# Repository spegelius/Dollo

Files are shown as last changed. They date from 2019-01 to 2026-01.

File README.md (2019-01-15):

# Dollo3D
A (almost) fully printed 3D printer, that scales.

# Goals in order of priority

1) Make a 3D printer that can make as many of its own parts as possible

2) Have it so the machine can scale with little to no throwing away of old parts

3) Make it easy to assemble

4) Use no more than a single 1KG spool of plastic to make. (not happening)

5) Make it as low cost as possible.

6) use parts that are easy to find.

7) make it durable (since it can print its own parts this isn't super high priority)

8) hope people stop asking "what if you could 3D print a 3D printer" because of course you can and its not that unique of an idea

# Part count and list for smallest viable Dollo, with around 21x21x12cm print volume. Smaller frame can be built, but the z-axis parts aren't tested in any way with that kind of setup

* 26 -- extention.stl
* 4 -- extention_90_bend.stl (or extention_90_bend_extra_stiff.stl)
* 8 -- corner.stl (or corner_extra_stiff.stl)
* 192+ -- bow_tie.stl but extra never hurts (or bow_tie_with_brim.stl)
* 132+ —- long_tie.stl (or long_tie_split.stl, more forgiving on the tolerances)
* 10+ -- long_tie_half.stl
* 50+ -- long_bow_tie.stl (or long_bow_tie_split.stl, more forgiving on the tolerances)
* 2 -- x_spacer.stl
* 6 -- rack_5.stl
* 6 -- rack_dove_pin.stl 
* 1 -- bed_carriage_endstop_screw.stl
* 1 -- bed_carriage_endstop_screw_mount.stl
* 1 -- bed_carriage_endstop_screw_nut.stl
* 4 -- bed_carriage_rail.stl
* 4 -- bed_carriage_rail_short.stl
* 4 -- bed_carriage_rail_center.stl
* 2 -- bed_carriage_rail_frame_mount.stl
* 2 -- bed_carriage_rail_frame_mount_top.stl
* 4 -- bed_carriage_rail_slide.stl
* 2 -- bed_screw_housing.stl
* 2 -- bed_screw_housing_coupler.stl
* 2 -- bed_screw_housing_top.stl
* 10+ -- cable_clip_large.stl/cable_clip_small.stl
* 1 -- cable_shroud_frame_mount.stl (if using cable shroud)
* 1 -- hot_end_mount.stl
* 1 -- hot_end_mount_clamp.stl (or hot_end_mount_clamp_shroud_mount.stl if using cable shroud)
* 1 -- hot_end_mount_fan_duct.stl
* 1 -- hot_end_mount_prox_sensor_clamp.stl (if using proximity sensor)
* 4 -- leg.stl
* 4 -- leg_foot.stl OR following 3 items.
* 4 -- leg_foot_adjustable.stl
* 4 -- leg_foot_adjustable_core.stl
* 4 -- leg_foot_dampener.stl (print with flex material)
* 3 -- motor_gear.stl (or motor_gear_slop_0.1.stl)
* 6 -- motor_mount_small.stl
* 1 -- psu_holder.stl OR following 3 parts if using ATX psu
* 1 -- psu_holder_atx_psu_cover.stl
* 1 -- psu_holder_back_atx.stl
* 1 -- psu_holder_front_atx.stl
* 1 -- psu_holder_clip_extension.stl
* 2 -- xy_endstop_rackend.stl OR
* 2 -- xy_endstop_racktop.stl (I prefer this, easier to adjust position)
* 1 -- z_endstop.stl
* 2 -- z_screw_120.stl
* 2 -- z_screw_center_coupler.stl
* 2 -- z_screw_motor_coupler_flex.stl
* 2 -- z_coupler_flexible_coupler_nut_hex.stl
* 2 -- z_coupler_flexible_coupler_tube.stl (print with flex material)
* 2 -- z_coupler_motor_shaft_adapter.stl
* 6 -- z_screw_housing_bolt_side.stl
* 6 -- z_screw_side_roller.stl
* 6 -- z_screw_side_roller_axle.stl
* 6 -- z_screw_side_roller_axle_washer.stl
* 1 -- ramps_mount.stl
* 2 -- ramps_mount_fan_mount_60mm.stl
* 3 -- ramps_mount_frame_clip.stl
* 2 -- tools/rail_jig.stl
* 2 -- tools/rail_jig_clip.stl
* 1 -- tools/z_screw_jig.stl
* 2 -- tools/z_screw_jig_clip.stl

# Metal parts we might get rid of in the future

* 9 -- M3x40  for the motor mounts
* 8 -- M3x10  for the z motors

# Electronics and other

* 1 - main controller board. Frame mount parts for RAMPS are available. Also for Raspi3
* 3 - end stop switches
* 5 - steppermotors , no need for very beefy motors
* 1 - hotend or whatever tool tip you want really. E3Dv6 is tested
* 1 - hobbed thing, gear or bolt. Actually whole extruder. Buy or pick one to print from thingiverse. This is good: https://www.thingiverse.com/thing:2243325
* 1 - heated bed (21x21cm)
* 1 - glass/aluminum that fits on the bed (depends if the bed needs one)
* 4 - springs and screw for leveling your bed.
* some glue for joining the bed_carriage_rail and z_screw parts together

# Options for a larger printer

* the default expansion length in each direction is 12cm (default extention part length).
* the frame can be extended in any direction, just print enough extention.stl parts and ties. If extending in z-direction, also print enough bed_carriage_rail, bed_carriage_rail_center, z_screw_120, z_screw_center
* the default 12cm expansion length can be adjusted to suit ones need, just modify the scad files and export different length models (make sure all updated models are same length)
* the frame will become somewhat wobbly after certain z-height (25+cm). There are stabilizer parts designed, but not for the current Dollo iteration. WIP currently

# Print settings
1. I use PLA for most of the parts, except PETG for rack_5, all _tie-parts and z_screw_side_roller. Flexible material (FilaFlex or similar) for few models (see BOM). Nylon for the part cooling (hotend) fan
2. For most parts, 2x perimeter, 20% infill, 0.2mm layer height, outer perimeter first and no supports. Some models do need supports, but those should be easy to spot.
3. Motor_gear: 4+ perimeters, 90% infill
4. bed_carriage_rails, centers, z_screws: 3 perimeters, 25+% infill
5. All _tie parts: print only after printing at least 1 extention. Print few of each _tie part and see how they fit. Most likely you'll need to use scaling in slicer sw to get them fit.

# How to assemble (mostly old info, needs update)
1) start with the basic frame, take a single corner and butt joint all 3 extension pieces to it with all 4 bow_tie slots. then on the end of each of those add corner pieces then extension pieces again until you have built out a full cube shape.

2) put on the racks. first you need to decide what side you want to be up, this really doesn't matter since it should be the same on all sides. Once you have figured that out, you can start putting your slots on the top of your printer with more bow ties add racks on parallel sides and to the top of your remaining extension piece. each should have 3 racks on it.

3) mounting your motors. first you will need to put a gear.scad on your motor shaft, then you can take a motor and put the motor_mount_small on it and screw in the single counter sunk screw on the bottom using a M3x10 and then put it on your printer rack and make sure the gear aligned with the rack teeth. once it does you can keep it on the rack and screw in your other motor_mount_small to the other side. (make sure to do this on the printer because if you don't it wont go on after) do this for all 3 racks and make sure the motor faces out.

4) mounting the x axis. grab your x_spacer and put them on the end of what you already have assembled on the left over extention piece and then slide that into the motor mount on each side of the printer.

5) Get the frame ready for the bed. first you need to prep you printer by taking the crazy looking twist_corner pieces and bow tie them to the inside of the printers frame mirroring each other but keep the bottom one out on each side.

6) now take a motor and mount put the gear_one on it and mount that to your bed, then take your middle_gear and put those next to the motor and then put your large_gear and large_twist together, and put those next in line. 

7) putting the bed in. This can be kind of tricky, but you have to twist your bed so it goes inside the frame sideways and the you should be-able to twist it to make it fit in the frame with the corners sticking out. and this is why we didn't put in the bottom corner_twists, because now your bed sits just under them and once you have the electronics set up it will be able to twist into those and once its in the teeth you will be able to add your last parts under it.

8) Electricity is fun. take all of your motor and put them into the correct stepper controllers making sure that your Y motors are plugged in opposite of each other. Plug in your electronics and make sure to upload the correct Dollo version of marlin. Once you have done this you should be able to move your motors and this is where you move your z motor in the negative direction (negative because that make the hotend and the bed closer) and once it is up at the top, you can put your last twist_corners on your printer.

9) hot ends and end stops. at the point of making this commit I do not yet have the end stops figured out. But the hotend should put in your hotend mount and should just slide and clip into your x motor mount. 

10) setting up the extruder. Not sure what extruder we are going to use yet, but if you have done 3D printing before you should know how all of that works and be able to get it going.

Z options) I do have the z axis all modeled for being fully printed and able to scale

# Extra cool facts

1) I came up with the original version of this when I was 16 and in high school and it was done in blender because thats all I knew how to use

2) This printer as it stands is under 1KG of printed parts 

3) We printed the first Dollo on 3 Prusa Mendal printer that were printer on other printers them selves and so on, all the way back to the start, so these machine have only open-source in their genealogy

4) I lived 300 miles from the printer that I used and did all of the printing over the internet using octopi to print the first Dollo

5) The Dollo can (if you want) have a metal core structure, we built it in just in case and it saved plastic so it was a win win.

6) The Dollo was made by a me and my dad, I didn't the modeling and he helped me come up with ideas on how to fix the issues I has on the way, and he test fit most of the pieces (the printers were at his house)

7) The Dollo has swappable tool heads so you can mill metal parts if you want!

8) We had no plans on how this was going to work before starting. We have gone through probably close to a 50 different ideas on how this thing should even work.

9) Half way though we almost gave up on the z and made the Dollo a Delta style printer (might still have something like that in the future)

10) We looked at a lot of other peoples printer before we could figure out how to do this one, we really could not have done it with out the community.

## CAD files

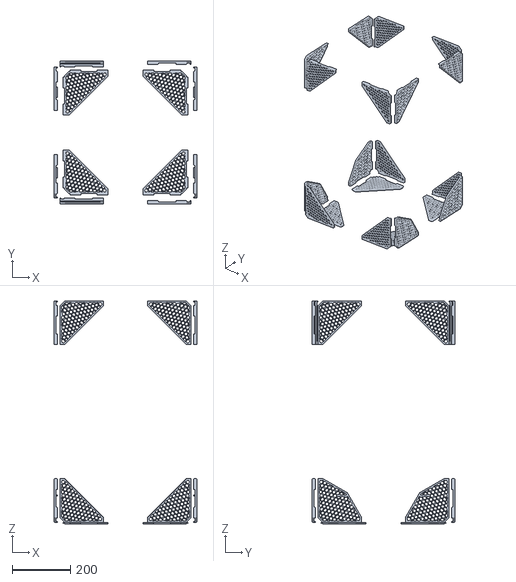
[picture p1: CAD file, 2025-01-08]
NEW_long_ties/mockup_stl/stabilizers_360_360_670_150.stl
490.0 x 490.0 x 766.0

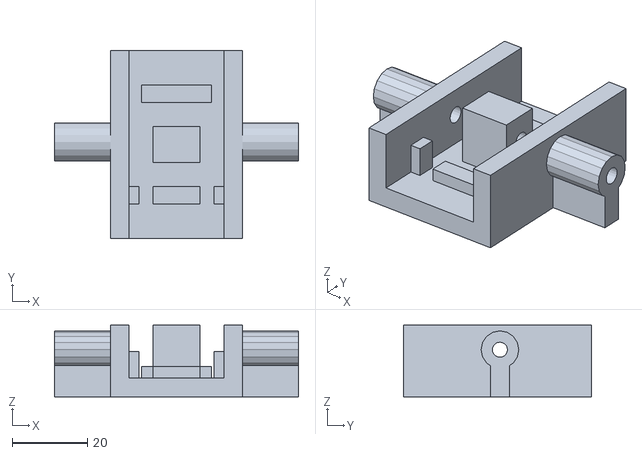
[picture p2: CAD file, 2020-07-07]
NEW_long_ties/STL/hacks/chain_link_drill_jig_4mm.stl
64.8 x 50.0 x 19.0

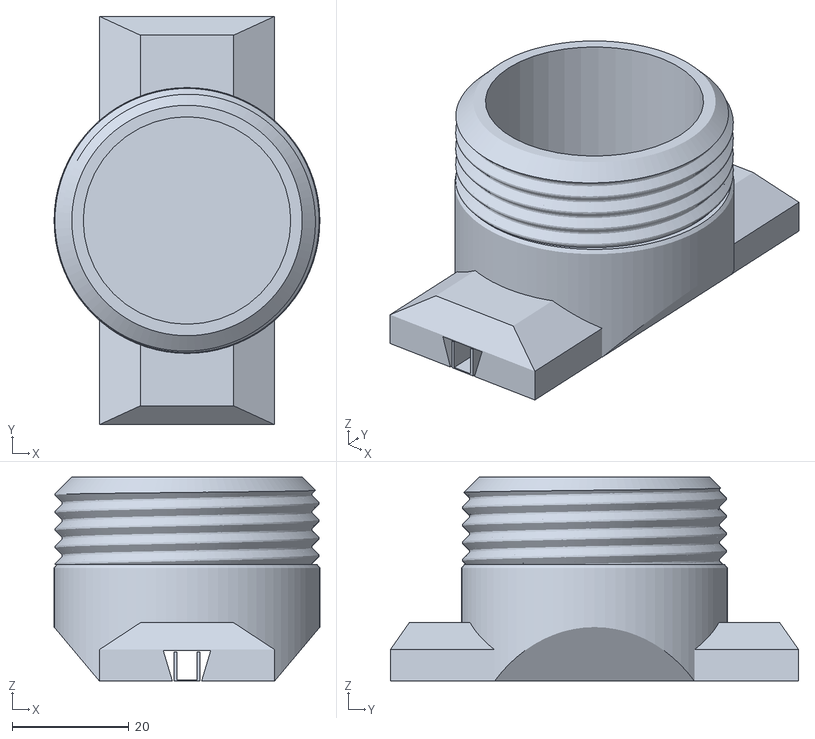
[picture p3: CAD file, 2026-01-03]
NEW_long_ties/STL/leg_middle_medium_adjustable.stl
45.6 x 70.0 x 35.0

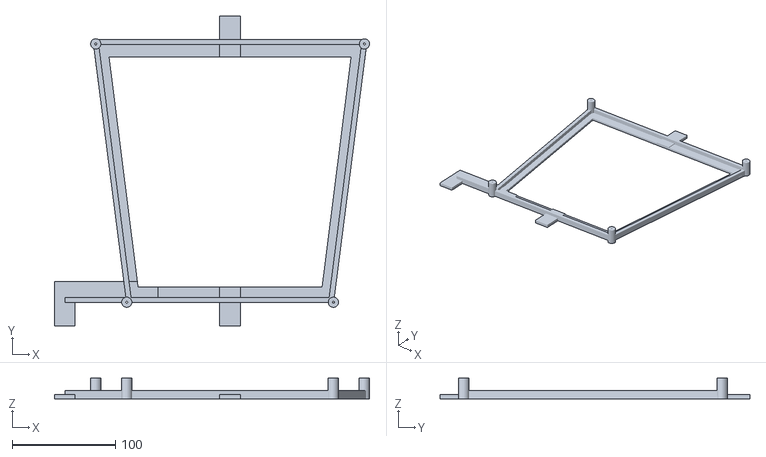
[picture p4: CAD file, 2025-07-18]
NEW_long_ties/STL/tools/bed_340_300_drill_jig.stl
305.0 x 300.0 x 20.0

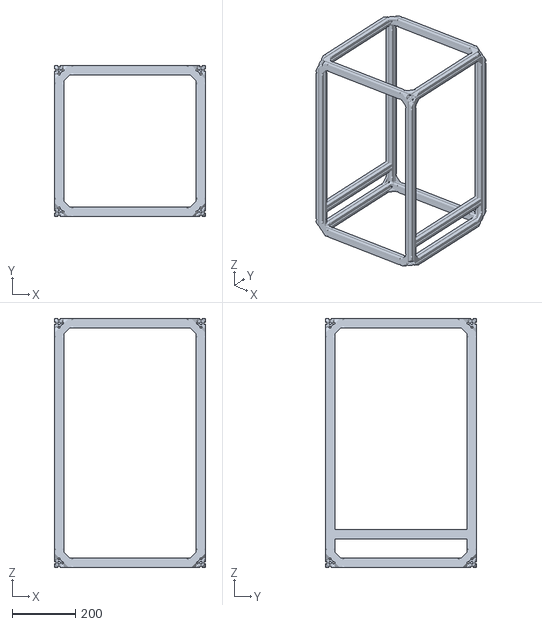
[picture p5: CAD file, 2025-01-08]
NEW_long_ties/mockup_stl/frame_360_360_670.stl
480.0 x 480.0 x 790.0

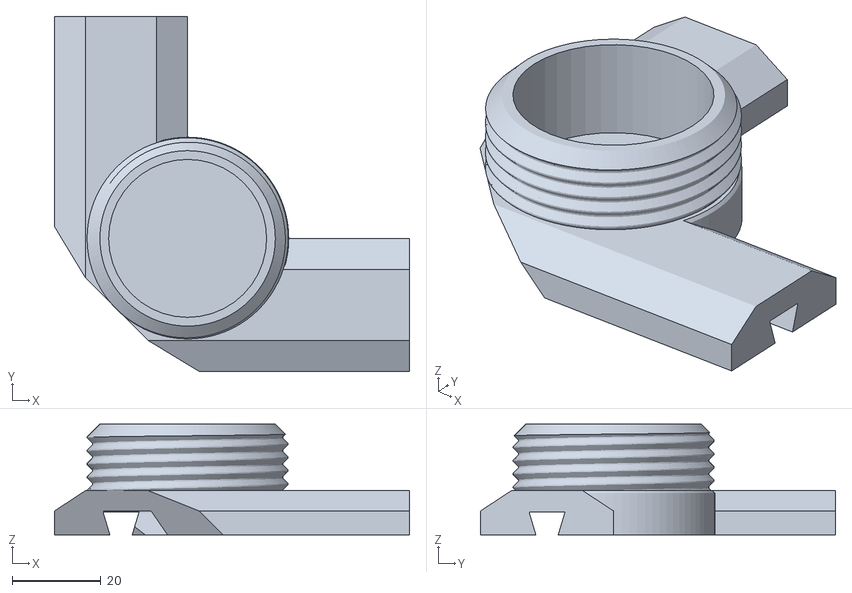
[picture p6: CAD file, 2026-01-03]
NEW_long_ties/STL/leg_small_adjustable_no_supports.stl
80.0 x 80.0 x 25.0

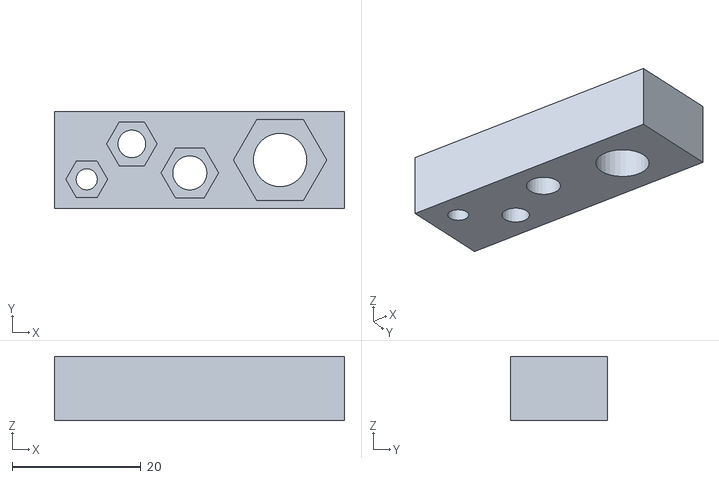
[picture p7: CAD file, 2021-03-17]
NEW_long_ties/STL/tools/test_nuts.stl
45.0 x 15.0 x 10.0

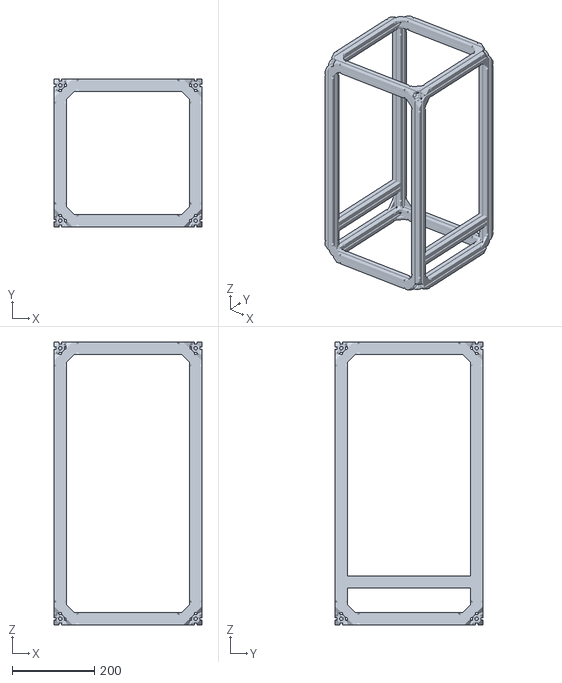
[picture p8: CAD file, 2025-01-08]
NEW_long_ties/mockup_stl/frame_240_240_570.stl
360.0 x 360.0 x 690.0

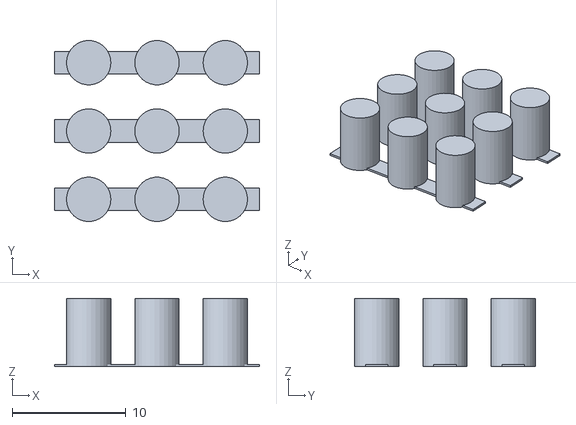
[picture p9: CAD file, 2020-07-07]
NEW_long_ties/STL/hacks/chain_link_drill_jig_nubs.stl
18.0 x 15.9 x 6.00

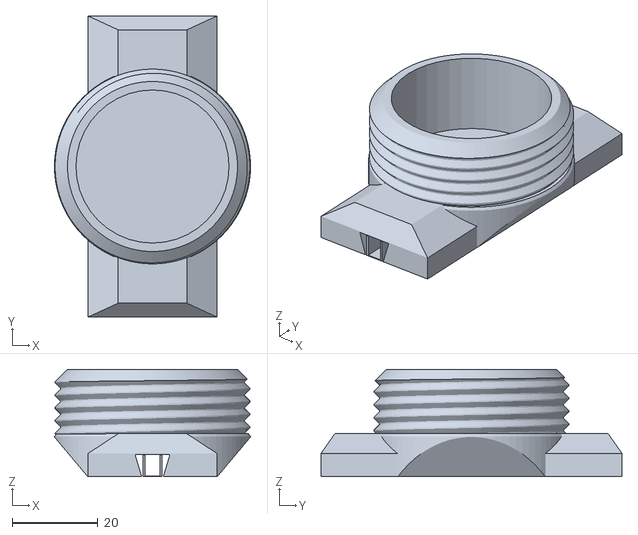
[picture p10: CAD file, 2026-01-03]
NEW_long_ties/STL/leg_middle_small_adjustable.stl
45.6 x 70.0 x 25.0

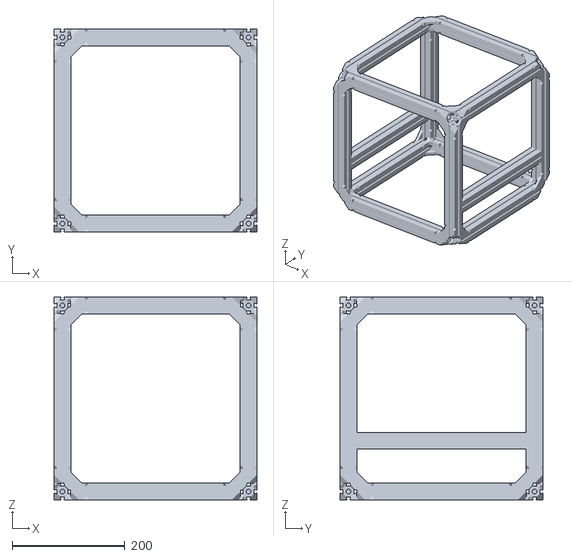
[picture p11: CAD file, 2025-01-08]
NEW_long_ties/mockup_stl/frame_240_240_240.stl
360.0 x 360.0 x 360.0

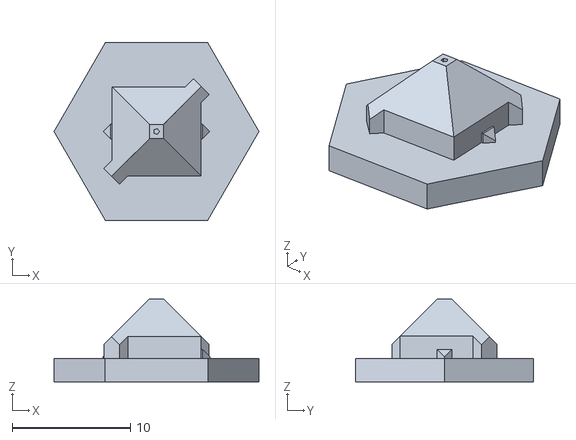
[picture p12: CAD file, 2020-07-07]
NEW_long_ties/STL/hacks/bed_carriage_rail_gap_plug.stl
17.3 x 15.0 x 7.00

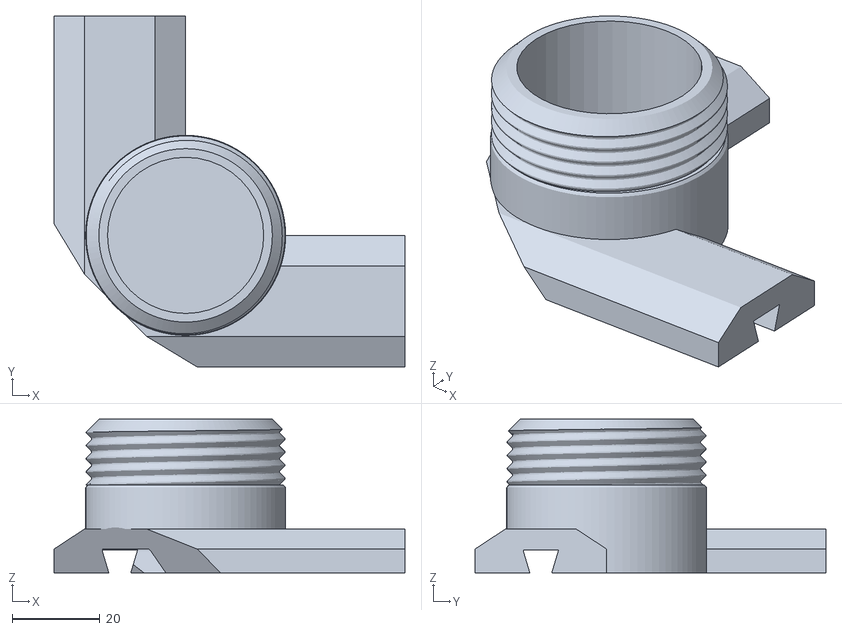
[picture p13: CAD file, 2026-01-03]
NEW_long_ties/STL/leg_medium_adjustable_no_supports.stl
80.0 x 80.0 x 35.0

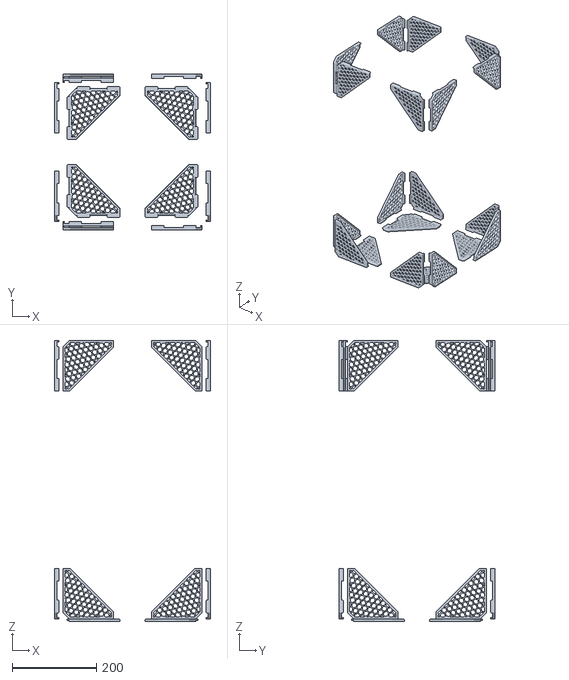
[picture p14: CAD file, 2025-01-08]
NEW_long_ties/mockup_stl/stabilizers_240_240_570_120.stl
370.0 x 370.0 x 666.0

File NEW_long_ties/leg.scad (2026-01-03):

include <globals.scad>;
include <include.scad>;

use <cable_clip.scad>;
use <extention.scad>;
use <mockups.scad>;
use <z_coupler.scad>;
use <z_screw.scad>;


////// VARIABLES //////

// core settings
pitch = 3;
dia_adjustable_inner = 45.9 - 0.3;
dia_adjustable_outer = 45.9 + 0.2;
echo("Adjustable dias:");
echo(dia_adjustable_inner, dia_adjustable_outer);

screw_steps = 100;


////// VIEW //////
//debug_leg_z();

//leg();
//leg_small_adjustable(render_threads=true);
//leg_small_adjustable(supports=false, render_threads=true);
//leg_small_adjustable(render_threads=false);

//leg_medium_adjustable(render_threads=true);
//leg_medium_adjustable(supports=false, render_threads=true);
//leg_medium_adjustable(render_threads=false);

//leg_middle_small_adjustable(render_threads=true);
//leg_middle_small_adjustable(render_threads=false);

leg_middle_medium_adjustable(render_threads=true);
//leg_middle_medium_adjustable(render_threads=false);

//leg_z();
//foot();
//foot_small();
//foot_adjustable_core();
//foot_adjustable();
//foot_dampener();

//test_adjustable_threads();


////// MODULES //////
module debug_leg_z() {
    intersection() {
        union() {
            leg_z();

            %translate([0, 0, 3*30 - motor_height/2])
            rotate([90, 0, 0])
            mock_stepper_motor(geared=false, center=true);
        }
//        translate([-50/2,0,0])
//        cube([50,50,200],center=true);
    }
}


module _leg_plate(length=40, height=10) {
    hull() {
        cube([30, length, height/2 + 0.4]);

        translate([(30 - 16)/2, 0, height/2])
        cube([16, length, height/2]);
    }
}

module _leg(units) {
    
    intersection() {
        translate([30/2, -30/2 + 30, units*30/2])
        extention(units=units + 1);

        cube([31, 31, 30*(units + 1)]);
    }
}

module _leg_dovetail(plate_len=50, bridge_extra=0.2) {
    translate([15, plate_len + 25, -0.01])
    rotate([90, 0, 0])
    male_dovetail(plate_len + 30, bridge_extra=bridge_extra);
}

module _leg_base_dovetails(plate_len=50, bridge_extra=0.2) {

    _leg_dovetail(plate_len=plate_len, bridge_extra=bridge_extra);

    mirror([1, 0, 0])
    rotate([0, 0, 90])
    _leg_dovetail(plate_len=plate_len, bridge_extra=bridge_extra);
}

module _leg_base(plate_len=50) {
    module _plates() {
        union() {
            translate([0, 10, 0])
            _leg_plate(plate_len + 10);

            translate([10, 30, 0])
            rotate([0, 0, -90])
            _leg_plate(plate_len + 10);
        }
    }

    difference() {
        union() {
            _plates();

            hull() {
                intersection() {
                    _plates();
                    cube([42, 42, 50], center=true);
                }
            }
        }

        _leg_base_dovetails(plate_len=plate_len);
    }
}

module _leg_support(plate_len=50) {
    plen = plate_len + 20;

    difference() {
        translate([15, plen/2, 5/2])
        cube([4.4, plen, 5], center=true);

        translate([15, plen/2, 5/2 + 0.2])
        cube([3.4, plen + 9, 5], center=true);
    }
}

module _leg_supports(plate_len=50) {

    _leg_support(plate_len=plate_len);

    mirror([1, 0, 0])
    rotate([0, 0, 90])
    _leg_support(plate_len=plate_len);
}

module leg(plate_len=50, units=3) {
    union() {
        _leg_base();
        _leg(units);

        // hole bridge
        translate([10, 10, male_dove_depth + 0.2])
        cube([10, 10, 0.2]);
    }
}

module _leg_adjustable(
    plate_len=60, height=10, supports=true, render_threads=true
) {
    difference() {
        union() {
            _leg_base(plate_len=plate_len);

            translate([30, 30, 0])
            hull() {
                cylinder(
                    d=dia_adjustable_inner, h=height - 0.6, $fn=80);
                cylinder(
                    d=dia_adjustable_inner - 1, h=height, $fn=80
                );
            }

            if (render_threads) {
                translate([30, 30, height - 0.01])
                v_screw(
                    h=15,
                    screw_d=dia_adjustable_inner,
                    pitch=pitch,
                    direction=0,
                    steps=screw_steps,
                    chamfer=true
                );
            } else {
                translate([30, 30, height - 2.01])
                chamfered_cylinder(
                    dia_adjustable_inner, 17, 1, $fn=30
                );
            }
        }

        difference() {
            _leg_base_dovetails(plate_len=plate_len, bridge_extra=0.4);

            translate([0, 200/2 + 22.5, 1/2 + 5.2])
            cube([50, 200, 1], center=true);

            translate([200/2 + 22.5, 0, 1/2 + 5.2])
            cube([200, 50, 1], center=true);
        }

        translate([30, 30, 7])
        cylinder(d=dia_adjustable_inner - 10, h=2*height, $fn=40);

        // chamfer
        //translate()
        rotate([0, -35, 45])
        cube([44, 60, 60], center=true);
    }

    if (supports) {
        difference() {
            _leg_supports(plate_len=plate_len);

            rotate([0, 0, 45])
            cube([44, 60, 60], center=true);
        }
    }
}

module leg_small_adjustable(
    plate_len=60, supports=true, render_threads=true
) {
    _leg_adjustable(
        plate_len=plate_len, height=10,
        supports=supports, render_threads=render_threads
    );
}

module leg_medium_adjustable(
    plate_len=60, units=3, supports=true, render_threads=true
) {
    _leg_adjustable(
        plate_len=plate_len, height=20,
        supports=supports, render_threads=render_threads
    );
}

module _leg_middle_adjustable(
    plate_len=70, height=10, supports=true, render_threads=true
) {
    difference() {
        union() {
            _leg_plate(length=plate_len);

            translate([15, 70/2, 0])
            hull() {
                cylinder(
                    d=dia_adjustable_inner, h=height - 0.6, $fn=80);
                cylinder(
                    d=dia_adjustable_inner - 1, h=height, $fn=80
                );
            }

            if (render_threads) {
                translate([15, 70/2, height - 0.01])
                v_screw(
                    h=15,
                    screw_d=dia_adjustable_inner,
                    pitch=pitch,
                    direction=0,
                    steps=screw_steps,
                    chamfer=true
                );
            } else {
                translate([15, 70/2, height - 2.01])
                chamfered_cylinder(
                    dia_adjustable_inner, 17, 1, $fn=30
                );
            }
        }

        _leg_dovetail(plate_len=plate_len);

        translate([15, 70/2, 7])
        cylinder(d=dia_adjustable_inner - 10, h=2*height, $fn=40);

        // chamfers
        translate([0, -16, 0])
        rotate([-35, 0, 0])
        cube([80, 20, 40], center=true);

        translate([0, 70  + 16, 0])
        rotate([35, 0, 0])
        cube([80, 20, 40], center=true);

        translate([-13.1, 0, 0])
        rotate([0, -40, 0])
        cube([20, 200, 40], center=true);

        translate([30 + 13.1, 0, 0])
        rotate([0, 40, 0])
        cube([20, 200, 40], center=true);
    }

    if (supports) {
        _leg_support(plate_len=plate_len - 20);
    }
}

module leg_middle_small_adjustable(render_threads=true) {
    _leg_middle_adjustable(
        plate_len=70, height=10, supports=true, render_threads=render_threads
    );
}

module leg_middle_medium_adjustable(render_threads=true) {
    _leg_middle_adjustable(
        plate_len=70, height=20, supports=true, render_threads=render_threads
    );
}

module leg_z() {

    module _z_leg() {
        difference() {
            union() {
                translate([0, 0, 30])
                extention(2);

                translate([0, 0, 38])
                hull() {
                    cube([30, 30, 1], center=true);

                    translate([0, 0, 15/2 + 10])
                    cube([
                        motor_side_length + 8,
                        motor_side_length + 8,
                        13
                    ], center=true);
                }
            }
            translate([0, 0, 50 + 1/2])
            hull() {
                cube([
                    motor_side_length,
                    motor_side_length, 1
                ], center=true);

                translate([0, 0, 30])
                cube([
                    motor_side_length - 2,
                    motor_side_length - 2, 1
                ], center=true);
            }

            translate([0, 0, 50 + 30/2])
            hull() {
                cube([
                    motor_side_length - 8,
                    motor_side_length - 8, 30
                ], center=true);

                cylinder(d=9, h=60, center=true);
            }

            translate([0, motor_side_length/2, 50 + 15/2])
            cube([17, 10, 15], center=true);
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

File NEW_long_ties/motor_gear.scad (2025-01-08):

include <globals.scad>;
include <include.scad>;
use <../snappy-reprap/publicDomainGearV1.1.scad>;
use <mockups.scad>;

////// VARIABLES //////
$fn=50;
obj_round = 50;
 // based on obj_height = 50 / twist=81
//obj_height = 20;

shaft = motor_shaft_hole_dia;

shaft_len = 22;
shaft_has_flat = true;
shaft_flat_len = 15;

// gear
twist = 25.9808;
twist_constant = rack_h/2/twist;
echo (6.4/twist_constant);

////// VIEW //////
//debug();

//motor_gear();
motor_gear(shaft_slop=0.1);


////// MODULES //////
function get_twist(obj_height, twist_ratio) = (twist_ratio == 1) ? 1 : obj_height * twist_ratio;

// deprecated
module gear_master(obj_height, twist_ratio){

	module rightGear(twist, obj_height) {
		rotate([0, 0, -25]) {
			translate([0, 0, obj_height/4])
			linear_extrude(
                height=obj_height/2,
                center=true,
                twist=twist,
                convexity = 10
             )
			import(
                file="small_gear.dxf",
                layer="Layer_1"
            );

			circle(r = 1);
		}
	}

    module gearObject(obj_height) {

        module gear(twist, obj_height) {
            union() {
                rightGear(twist, obj_height);

                mirror([0, 0, 1])
                rightGear(twist, obj_height);
            }
        }

        module bone(obj_height) {
            twist = get_twist(obj_height, twist_ratio);
            echo(twist);
            difference() {
                gear(twist, obj_height);
                hole(obj_height);
            }
        }
        bone(obj_height);
    }
    gearObject(obj_height);
}

// shaft hole
module hole(obj_height) {
    cylinder(
        d=shaft, h=obj_height*2.1,
        center=true, $fn=50
    );
}

module bolt_hole(bolt_size, obj_height) {

    rotate([0,90,0])
    cylinder(
        d=bolt_size, h=20, center=true, $fn=50
    );

    translate([18/2 - 2.3, 0, 0])
    rotate([0, 90, 0])
    cylinder(d1=3, d2=7.8, h=2.4, $fn=50);

    translate([-18/2 + 2.3, 0, 0])
    rotate([0, -90, 0])
    cylinder(d1=3, d2=7.8, h=2.4, $fn=50);
}


module motor_gear(
    nut_size=m3_nut_side, nut_height=m3_nut_height,
    bolt_size=bolt_hole_dia, shaft_slop=0
) {

    difference() {
        difference() {
            union() {
                // bottom body
                hull() {
                    translate([0, 0, 1])
                    cylinder(d=18, h=6.61, $fn=50);

                    cylinder(d=16, h=8.61, $fn=50);
                }

                // lower gear half
                translate([0, 0, 11.8])
                gear (
                    mm_per_tooth = rack_tooth,
                    number_of_teeth = 8,
                    thickness = 6.4,
                    hole_diameter = 2,
                    twist = 6.4/twist_constant,
                    teeth_to_hide = 0,
                    pressure_angle = 19,
                    backlash = 0
                );

                // upper gear half
                translate([0, 0, 17.99])
                mirror([0, 0, 1])
                gear (
                    mm_per_tooth = rack_tooth,
                    number_of_teeth = 8,
                    thickness = 6,
                    hole_diameter = 2,
                    twist = twist,
                    teeth_to_hide = 0,
                    pressure_angle = 19,
                    backlash = 0
                );

                // internal body
                translate([0, 0, 7])
                cylinder(
                    d=motor_shaft_hole_dia + 4.6,
                    h=13.99, $fn=50
                );

                // smol internal body
                translate([0, 0, 7])
                cylinder(
                    d=motor_shaft_hole_dia + 3,
                    h=14.99, $fn=50
                );
            }
            translate([0, 0, -0.1])
            rotate([0, 0, -90])
            motor_shaft(
                h=22, extra_slop=shaft_slop, $fn=50
            );

            cylinder(d1=5.6, d2=5, h=0.6, $fn=50);

            union() {
                difference() {
                    translate([0, 0, 21.5])
                    cylinder(
                        h=3, d=20,
                        center=true, $fn=50
                    );

                    translate([0, 0, 20.5])
                    cylinder(
                        h=2 + 0.05, d1=20,
                        d2=8, center=true, $fn=50
                    );
                }
            }
        }
        translate([0, 0, 5])
        bolt_hole(bolt_size - 0.15, 21);

        translate([shaft/2 + 0.8, 0, 4/2 + 1])
        rotate([0, 90, 0])
        elongated_nut(4, cone=false);

        translate([
            -shaft/2 - 0.8 - nut_height,
            0, 4/2 + 1
        ])
        rotate([0, 90, 0])
        elongated_nut(4, cone=false);
    }
}

module debug() {
    rotate([90, 0, 0])
    mock_stepper_motor(center=true);

    translate([0, 0, 22])
    intersection() {
        rotate([0, 0, 90])
        motor_gear(shaft_slop=0.1);

        translate([30/2, 0, 30/2])
        cube([30, 30, 30], center=true);
    }
}

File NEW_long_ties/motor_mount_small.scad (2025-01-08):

$fn = 30;
include <globals.scad>;
include <include.scad>;


////// VARIABLES //////
frame_width = 35.5;
tail_depth = 11;
rack_height = 12.5;
rack_slide_height = 8;
mount_max = 62.5;
wabble = 1.5;
not_tooth_gap = 0;
rack_gap = 2.5;
tower_height = 17.5+3;

text = "Dollo";
font = "Liberation Sans";

hole_length = 1;

//$fn=220;

// for rounded cube
diameter = 2;

////// DEBUG /////
assembly_motor_mount();

////// VIEW //////
//motor_mount(bridges=true);
//motor_mount(bridges=true, motor_side=false);


////// MODULES //////
module assembly_motor_mount() {
    render()
    translate([0, -24.1, 13.1])
    rotate([-90, 0, 0])
    motor_mount(bridges=false, motor_side=false);

    render()
    mirror([0, 1, 0])
    translate([0, -24.1, 13.1])
    rotate([-90, 0, 0])
    motor_mount(bridges=false);
}


module y_mount_added(motor_side){    
    //base
    translate([0, -5.75 + rack_gap/2, -1])
    rounded_cube(
        y=38.5 + rack_gap * 2, x=frame_width + 35 + 1,
        z=4, center=true, corner=diameter
    );
    
    // lower slide
    slide_depth = 11;
    slide_pos_y = frame_width - 24.9 + rack_gap;
    
    module slide() {
        difference() {
            rotate([45, 0, 0])
            rounded_cube(
                z=15, x=17, y=15,
                corner=2, center=true
            );

            translate([0, 0, -8])
            cube([60, 30, 30], center=true);
        }
    }
    
    translate([-27, slide_pos_y, -4.55])
    slide();

    translate([0, slide_pos_y, -4.55])
    slide();

    translate([27, slide_pos_y, -4.55])
    slide();
    
    translate([0, slide_pos_y - 8.85, 0.6])
    rounded_cube(
        z=5, x=frame_width + 35 + 1, y=26,
        corner=diameter, center=true
    );

    if (motor_side) {
        translate([0, slide_pos_y, 0.05])

        hull() {
            rounded_cube(
                z=6.1, x=10, y=28, corner=diameter,
                center=true
            );

            translate([0, -28/2 + 2/2, 0])
            rounded_cube(
                z=6.1, x=35, y=2, corner=diameter,
                center=true
            );
        }

    }

    // center
	translate([-11, -12.75, 0.625])
    cube([22, 18, 10]);

    // towers

    //top tower
	translate([0 - 21, -25.75, 0.625])
    cube([42, 18, tower_height]);
    
    tower_pos_y = -2;

    // right tower
	translate([20, tower_pos_y, (17.5 + 4.25)/2])
    rounded_cube(20, 15, tower_height, diameter, center=true);

    translate([
        (32  -21 - 4) + 19 - 4.5,
        tower_pos_y + 15/2 - 4.8,
        tower_height]
    ) 
    cylinder(d=7, h=2);
    
    // left tower
    difference() {
        translate([-20, tower_pos_y, (17.5 + 4.25)/2])
        rounded_cube(
            20, 15, tower_height,
            diameter, center=true
        );

        translate([
            (-21 - 4) + 3.5, tower_pos_y + 15/2 - 4.8,
            tower_height-1.5]
        )
        cylinder(d=7.25, h=2.5, $fn=30);
    }
}

module bolt_hole() {
    hull() {
        cylinder(d=bolt_hole_dia, h=70, $fn=30);

        translate([hole_length, hole_length, 0])
        cylinder(d=bolt_hole_dia, h=70, $fn=30);
    }
}

module bolt_head_hole() {
    hull() {
        cylinder(d=6.5, h=3, $fn=30);

        translate([hole_length, hole_length, 0])
        cylinder(d=6.5, h=3, $fn=30);
    }
}

module tapered_bolt_head_hole() {
    hull() {
        cylinder(
            d1=bolt_hole_dia, d2=6.5, h=3, $fn=30
        );

        translate([hole_length, hole_length, 0])
        cylinder(
            d1=bolt_hole_dia, d2=6.5, h=3, $fn=30
        );
    }
}

module y_mount_taken(bridges, motor_side){

    function bolt_hole_h() = bridges ? 0.2 : 0;

	halign = [
	   [0, "center"]
	 ];
	 
    rotate([0, 0, -90])
    for (a = halign) {
        translate([-6.5, 12, -3])
        linear_extrude(height = 1)
        text(
            text = str(text), font = font,
            size = 6, halign = a[1]
        );
    }
    rotate([0, 0, 90])
    for (a = halign) {
        translate([6.5, 12, -3])
        linear_extrude(height = 1)
        text(
            text = str(text), font = font,
            size = 6, halign = a[1]
        );
    }
		 
	rotate([0, 0, 45]) {
        // bolt holes. leave 0.2 = one layer which can be easily drilled out
        translate([
            5.65 - 21, 5.65 - 21, bolt_hole_h()
        ])
        bolt_hole();

		translate([
            5.65 + 31-21, 5.65 - 21, bolt_hole_h()
        ])
        bolt_hole();

		translate([
            5.65 - 21, 5.65 + 31 - 21, bolt_hole_h()
        ])
        bolt_hole();

		//counter sink
        translate([5.65 - 21, 5.65 - 21, -3])
        bolt_head_hole();

		translate([5.65 + 31 - 21, 5.65 - 21, -3])
        bolt_head_hole();

        translate([5.65 - 21, 5.65 + 31 - 21, -3])
        bolt_head_hole();


        if (motor_side) {
            translate([
                5.65 + 31 - 21, 5.65 + 31 - 21, -10
            ])
            bolt_hole();

            translate([
                5.65 + 31 - 21, 5.65 + 31 - 21, 0.5
            ])
            tapered_bolt_head_hole();
        }

        // large chamfers
        difference() {
            translate([-70, -30, -5])
            cube([50, 70, 50]);

            translate([-19, -7, 0])
            rotate([0, 0, 45])
            rounded_cube(12, 12, 100, 3, center=true);
        }
        difference() {
            translate([-30, -70, -5])
            cube([70, 50, 50]);

            translate([-7, -19, 0])
            rotate([0, 0, 45])
            rounded_cube(12, 12, 100, 3, center=true);
        }

        // motor center hole
        if (motor_side) {
            translate([0, 0, -5])
            hull() {
                cylinder(d=motor_center_hole, h=4);
                cylinder(
                    d=motor_center_hole - 8, h=18
                );

                translate([
                    hole_length, hole_length, 0
                ]) {
                    cylinder(
                        d=motor_center_hole,
                        h=4, $fn=30
                    );

                    cylinder(
                        d=motor_center_hole - 8,
                        h=18, $fn=30
                    );
                }
            }
        }

        // dove holes
        if (!motor_side) {
            rotate([90, 0, -45])
            translate([-8, -3, -43 + tail_depth])
            male_dovetail(height=30, bridge_extra=0.2);

            rotate([90, 0, -45])
            translate([8, -3, -43 + tail_depth])
            male_dovetail(height=30, bridge_extra=0.2);
        }

		rotate([90, 0, -45])
        translate([-8, -3, 22 - tail_depth])
        male_dovetail(height=30, bridge_extra=0.2);

		rotate([90, 0, -45])
        translate([8, -3, 22 - tail_depth])
        male_dovetail(height=30, bridge_extra=0.2);
	}
}

module _motor_mount(bridges, motor_side){
	difference(){
		y_mount_added(motor_side);
		y_mount_taken(bridges, motor_side);
	}
}

module translated_mount(bridges, motor_side){
    translate([(-obj_leg/2) - 2.5, 0, 0])
    rotate([0, 90, 0])
    _motor_mount(bridges, motor_side);
}

module motor_mount(bridges=true, motor_side=true) {
    translate([0, 0, 20.5])
    rotate([0, -90, 0])
    difference(){
        translated_mount(bridges, motor_side);

        translate([-15, 0, 0])
        rotate([0, 90, 0])
        union(){
            translate([-20, 20, 15])
            rotate([90, 0, 45])
            cylinder(h=70, d=22, $fn=40);

            translate([20, 20, 15])
            rotate([90, 0, -45])
            cylinder(h=70, d=22, $fn=40);
        }
    }
}

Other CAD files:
NEW_long_ties/STL/hacks/chain_link_drill_jig.stl
NEW_long_ties/STL/hacks/rail_center_quickfix_joiner2.stl
NEW_long_ties/STL/leg_medium_adjustable.stl
NEW_long_ties/STL/tools/rail_jig_clip.stl
NEW_long_ties/slop_calibration.scad
NEW_long_ties/STL/adapter_SSR_1048ZD3.stl
NEW_long_ties/STL/adapter_SSR_1048ZD3_cover.stl
NEW_long_ties/STL/adapter_airtrippers_bowden_extruder.stl
NEW_long_ties/STL/adapter_dove_m3_15.stl
NEW_long_ties/STL/adapter_dove_m3_28.stl
NEW_long_ties/STL/adapter_mks_sbase_box.stl
NEW_long_ties/STL/adapter_shy_rockabilly.stl
NEW_long_ties/STL/adapter_shy_rockabilly2.stl
NEW_long_ties/STL/adapter_shy_rockabilly2_m3.stl
NEW_long_ties/STL/adapter_shy_rockabilly3.stl
NEW_long_ties/STL/adapter_titan.stl
NEW_long_ties/STL/adapter_tl_smoother.stl
NEW_long_ties/STL/bed_adjustment_nut.stl
NEW_long_ties/STL/bed_adjustment_nut_M4.stl
NEW_long_ties/STL/bed_attachment_clip_side_1.stl
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

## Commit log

2016-09-30 Fix twist corner scaling and regen STL
    [twist_corner.scad, twist_corner.stl]
2016-09-30 Gears gears gears
    - 'OLd' folder dxf files
    - make gear teeth smaller, maybe run more smoothly. NOT TESTED
    - paying around with new layout of gears in bed, future dev...
    - add new gear_one that has some extra body arounf the stepper
    motor shaft
    [gear.dxf, gear_one_with_extra_body.stl, gears.scad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]
2016-09-30 Stabilizer updated, add twist_corner_riser model
    - twist_corner_riser was needed to proper set the twist_corner
    position regards the bed
    [stabilizer.scad, stabilizer.stl, twist_corner_riser.scad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]
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2016-09-30 Hack model added
    - broke my bed carriage, quickfixed it
    [bed_carriage_quickfix.scad]
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2016-09-30 Update long_tie models
    - make long_tie configurable when used in other
    models
    - make half bow_tie use long_bow_tie model
    - regen stls
    [long_bow_tie.scad, long_bow_tie.stl, long_bow_tie_half.scad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]
2016-10-11 Bed carriage threaded z, globals
    - RC quality parts
    - add threaded rod values to globals
    [bed_carriage_threaded_z.scad, bed_carriage_threaded_z.stl, globals.scad]
2016-10-23 Refactoring, inheritance
    - moved some generic functions and variables to
    include and globals
    - threaded z: designed rod quide that attaches to side
    extension
    - regenerated some STLs
    [bed_carriage.scad, bed_carriage.stl, bed_carriage_threaded_z.scad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]
2016-10-23 Fix small error in rack
    - teeth were not exactly divisible by 30, instead it's
    29.93
    - some refactoring to calculations
    [rack.scad, rack.stl, rack_8.stl]
2016-10-23 Update z endstop holder
    - new version, lowered original for threaded z
    [z_endstop_holder.scad, z_endstop_holder.stl]
2016-10-26 New style rack and matching gear + mount
    - redesigned rack to have smaller gear track, because
    it seemed that long gearing was causing some unwanted
    twisting on X-axis
    - also made the areas that slide against motor mount smaller, hoping
    for less friction. Time will tell if this is good idea or not
    - recalculated mount diemnsions to better match the actual rack
    height
    - first test print: X moves a lot smoother than before, but there's
    still bit of twisting as the mount moves around. Maybe change
    gearing to have straight teeth
    [gear.scad, gear.stl, gearv2.stl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]
2016-11-08 Rework of rack and related parts
    - rack now uses gearing from snappy
    - needs still more work, but getting quite good prints
    already
    [endstop.scad, endstop_v2.stl, gear.scad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]
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2016-11-08 Experimental type long bow tie
    - should be more accommodating with slots that
    aren't as uniform, especcially if printed with
    bit more flexible material that PLA. PETG seems to
    work well
    [long_bow_tie_experimental.scad, long_bow_tie_experimental.stl]
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2016-12-12 Refactoring of long bow ties
    - scaling now comes from globals
    - most ties now use long_bow_tie as base
    [globals.scad, include.scad, long_bow_tie.scad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]
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2016-12-13 Improve hot end mount
    - proper hole size for hot end
    - better ties on the side
    - added clamp for securing the mount
    [hot_end_mount.scad, hot_end_mount.stl]
2016-12-13 New models to threaded z bed setup
    - a rail model with slide
    - frame attachment for securing the rails
    - a slide cradle for threaded rod and bed
    [bed_carriage_threaded_z.scad, bed_carriage_threaded_z_rail_holder.stl, bed_carriage_threaded_z_rail_slide.stl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]
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2017-01-21 Make framo mock size configurable
    - size in units, one unit = 12cm
    [include.scad]
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2017-01-21 Tighter gear center hole
    [gear.scad, gearv3.stl]
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2017-01-25 WIP: slop calibration
    [slop_calibration.scad]
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2017-02-25 Lots of updates
    - changed rounded_cube to require diameter argument -> changes
    needed to other modules
    - updated hot end mount to match newer motor mount
    - added stabilizer center parts
    [bed_carriage_threaded_z.scad, hot_end_mount.scad, hot_end_mount.stl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]
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2017-05-04 Hot end mount, mockups
    - add prox sensor mount
    - add fan duct
    - add mount parts for fan duct
    - add some mockups for e3dv6 and prox sensor
    [hot_end_mount.scad, hot_end_mount.stl, hot_end_mount_clamp.stl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]
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2017-05-04 Nuts and bolts
    - add some global variables for bolts
    - make nut model more configurable
    [globals.scad, include.scad]
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2017-05-04 Stabilzer parts update
    - use smaller diameters
    - add some frame clips for middle of the frame
    [stabilizer_center.scad, stabilizer_center_clip_nut.stl, stabilizer_center_frame_clip.stl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]
2017-09-14 Some majo change to rack, cannot remember what
    - probably the tie groove on top and some fine tuning of the
    side grooves
    [rack.scad, rackv4_4.stl]
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2018-01-30 Tune gear bolt dimension to tighter
    [gear.scad, gearv3.stl]
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2018-01-30 Tune motor shaft tighter; missing from gear update
    [globals.scad]
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2018-01-30 Motor mount: wider for more stability
    [motor_mount_small.scad]
2018-01-30 Slop calibration WIP
    [slop_calibration.scad]
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2018-02-06 Update bow_tie.scad
    fix reference to long_bowtie_experiential.scad
    [bow_tie.scad]
2018-02-07 Update bow_tie.scad
    fix references to long_bowtie_experiential.scad
    [bow_tie.scad, hot_end_mount.scad, psu_holder.scad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]
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2018-02-07 Rack and motor mount tuning
    - rack: slight adjustment of the side indent
    - motor mount: matc rack adjustment. Also move the model
    to z 0 and make the bolt holes slightly smaller
    [motor_mount_small.scad, motor_mount_small.stl, motor_mount_small_v3.stl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]
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2018-02-17 Rack: improve dove joints, finetuning
    - correct dovetail positions and sizes. Also
    add mechanism for locking the doves with a pin
    - add some extra room for the center dovetail indent to
    help with bridging
    [rack.scad, rack_4.stl, rack_5.stl]
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2018-03-05 Hot end mount update
    - change cooling fan mount mechanism
    - more parts in assembly preview
    [hot_end_mount.scad, hot_end_mount.stl]
2018-03-05 XY endstop update
    - endstop holders for attaching to rack end and top of rack
    - remove old models
    [endstop.scad, endstop.stl, endstop_v2.stl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]
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2018-03-05 Fast render mode for rack, for mock usage
    - also make rack size properly parametrized for
    external use
    [rack.scad]
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2018-03-05 Bed carriage rewrite WIP, rail update
    - rail: make size more configurable
    - also change the rail center part to have a notch for
    orientation
    - bed carriage: rewrite using extentions
    [bed_carriage.scad, bed_carriage_corner.stl, rail.scad]
2018-03-14 Common functions updated
    - proper thread length
    - added cube donut module
    - proper bed hole positions in frame mockup
    [include.scad]
2018-03-14 Remove missing include
    [stabilizer_center.scad]
2018-03-14 WIP: Z screw contraption
    - models for z-screw, side screws, screw housing and
    all needed parts
    [z_screw.scad]
2018-03-16 Z screw fixes
    [z_screw.scad]
2018-03-18 Fix slicing issues with KISSlicer
    Add tiny amount of overlap to base cube shaps, fixing slicing issues in KISSlicer.
    [corner.scad]
2018-03-18 Add supports for center of corner
    Add in support pillars for the overhangs in the center cutout.
    [corner.scad]
2018-03-29 Fix outset application
    Fix to apply outset to correct dimensions on each leg.
    [corner.scad]
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2018-05-20 Z-screw updates
    - new version of screw with gearing
    - updated center
    - flex version of motor coupler
    [globals.scad, z_screw.scad, z_screw_center.stl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]
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2018-05-20 Z-coupler update
    - add flexible coupler flex tube
    - update motor shaft adapter
    - add nut for clamping the tube over the motor adapter
    [z_coupler.scad, z_coupler_flexible_coupler_nut.stl, z_coupler_flexible_coupler_nut_hex.stl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]
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2018-07-06 Re-commit z-screw_120 as it was broken
    [z_screw.scad]
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2018-07-14 Fix E3Dv6 mockup dimensions
    - update also part cooling fan dimensions
    [hot_end_mount.scad, mockups.scad]
2018-07-24 Hot end mount QnD fix part and fan duct model
    [hot_end_mount.scad, hot_end_mount_fan_duct.stl]
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2018-08-22 Add corner with extra stiffness
    [corner.scad, corner_extra_stiff.stl, corner_extra_stiff_supports.stl]
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2018-08-22 Update motor gear
    - add bit more room for the rack, previous version was hitting
    on the rack thread
    - remove duplicate code
    - add model with 0.1mm slop in the motor shaft
    [motor_gear.scad, motor_gear_slop_0.1.stl]
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2018-08-22 Add missed adjustable foot stl
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2018-08-22 Add missed z screw jig clip stl
    [z_screw_jig_clip.stl]
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2018-08-25 Bed carriage housing update
    - tune tolerance for slides
    - regen housing and center stls
    [bed_carriage.scad, bed_carriage_rail.stl, bed_carriage_rail_center.stl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]
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2018-08-28 Z screw and bed carriage updates
    - screw housing slide holder tolerance to 0
    - screw housing slide holder 5mm taller
    - z screw side roller smaller tolerances
    - update housing screw
    [bed_carriage.scad, z_screw.scad, z_screw_center.stl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]
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2018-08-30 Extention updates
    - add 180 cm version
    - make 90 bend part more robust. Also add extra stiff version
    - experimental extention center part
    [bed_carriage_corner.stl, extention.scad, extention.stl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]
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2018-08-31 Update bed_carriage
    - rail mount holes: no slop, add a gap for allowing the hole
    to stretch
    [bed_carriage.scad, bed_carriage_rail_frame_mount.stl, bed_carriage_rail_frame_mount_top.stl]
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2018-09-08 Bit more stiff center parts
    [bed_carriage_quickfix.scad, bed_carriage_rail_center.stl, rail.scad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]
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2018-10-08 Corner: support and stiffness arguments
    [corner.scad]
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2018-12-01 Update corner 90 models
    - add hidden infill to the stiffener beam
    - add vertical beam for long corners
    [corner.scad, corner_90.stl, corner_90_20.stl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]
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2019-02-15 Rail slide: fixed slide spring size
    [rail.scad]
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2019-10-20 Extention reinforcement
    - add bit of forced perimeters to extention model
    [extention.scad, extention.stl, extention_150.stl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]
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2020-04-18 Tune endstops
    - some fixes to code
    - z endstop tuning
    [endstop.scad, xy_endstop_rackend.stl, xy_endstop_racktop.stl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]
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2020-04-18 Fixes to rounded_cube
    [include.scad]
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2020-05-24 Fix ATX psu back part dove position
    [psu_holder.scad, psu_holder_back_atx.stl]
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2020-11-30 Extention: glue version, infill fix
    [extention.scad, extention.stl, extention_150.stl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]
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2021-03-17 Extention t support fix
    [extention.scad, extention_t.stl]
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2021-11-27 Extention code style + fixes
    [extention.scad, extention.stl, extention_center_120_30.stl]
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2021-11-27 Motor mount update
    - fine tune the sliders
    - separated mounts so that the motor side mount has the lower
    part with the motor bolt hole. The other side doesn't have
    this part, which allows the whole to be slid off the Y-rail
    without disassembling the whole mount
    [motor_mount.stl, motor_mount_motor_side.stl, motor_mount_small.scad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]
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2023-01-26 Z coupler snd screw mall syntax fix
    [z_coupler.scad, z_screw.scad]
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2023-11-21 Extention and corner updates
    - changed to metric threaded rod for extentions and corners
    (8.3 mm)
    - extention_t dove hole tuning
    - bigger corner part
    - reworked corner supports
    [corner.scad, corner.stl, corner_75_extra_stiff_supports_side_supports.stl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]
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2025-01-08 chore: missing z motor models
    [z_motor_mount_no_supports.stl, z_motor_support_base.stl, z_motor_support_nut.stl]
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2025-01-08 chore: missing extention stl
    [extention_center_d_9.stl]
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2025-01-08 fix: mockups
    [mockups.scad]
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2025-01-08 fix: missing stl
    [raspberry_pi_3b_mount.stl, z_motor_mount.stl]
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
